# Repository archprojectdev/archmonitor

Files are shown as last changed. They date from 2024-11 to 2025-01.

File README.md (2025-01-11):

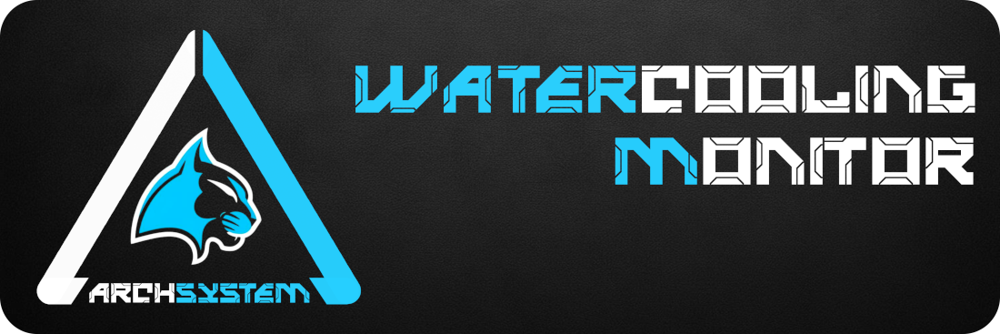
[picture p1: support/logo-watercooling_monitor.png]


Archmonitor est un module de gestion autonome de refroidissement liquide. 
Cette première version beta fonctionne sur un `Raspberry PI 4B` et prend en charge la configuration suivante :

- Deux pompes
- Deux sondes pour la température de liquide
- Une sonde pour le boitier
- Trois circuits indépendants de cinq ventilateurs
- Un circuit global `ARGB2`
- Un écran tactile de contrôle

Les configurations possibles sous cette version sont de :

- Deux modes de refroidissement configurable
- Trois modes configurables pour le circuit `ARGB2`

Le logiciel Archmonitor est basé sur la surcouche `ArchGUI` lui-même basé sur `FreeSimpleGUI` et sur `ws2812.py`. 
Ce programme fonctionne sur un `Raspberry PI 4B` avec le dernier `Raspberry Pi OS 64Bits` comme OS.<br/><br/>

⚠️ Ce module est encore en phase beta. De nombreuses améliorations et possibilités vont être apportées dans les mois à venir.<br/><br/>
Les améliorations déjà prévues sont : 

- Une configuration de plusieurs modes lumineux supplémentaires directement via l’écran tactile.
- Une gestion des modes lumineux par rapport au démarrage et à l’arrêt de l’ordinateur.
- Configuration des modes `silent` et `performance` via l’écran tactile.
- Démarrage de l’ordinateur via l’écran tactile.
- Ajout d’un second circuit ARGB2 pour avoir deux gestions lumineuses en tandem.
- Ajout d’un second écran pour l’affichage de données ou personnage animé.

<br/>

| Boitier prototype fermé | Boitier prototype ouvert |
|---|---|
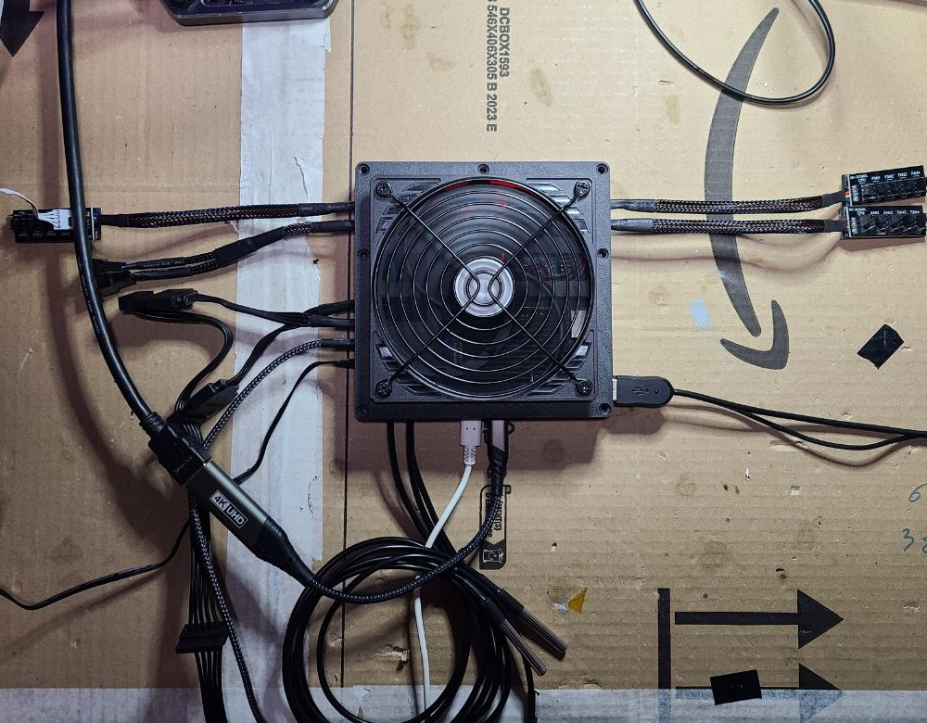
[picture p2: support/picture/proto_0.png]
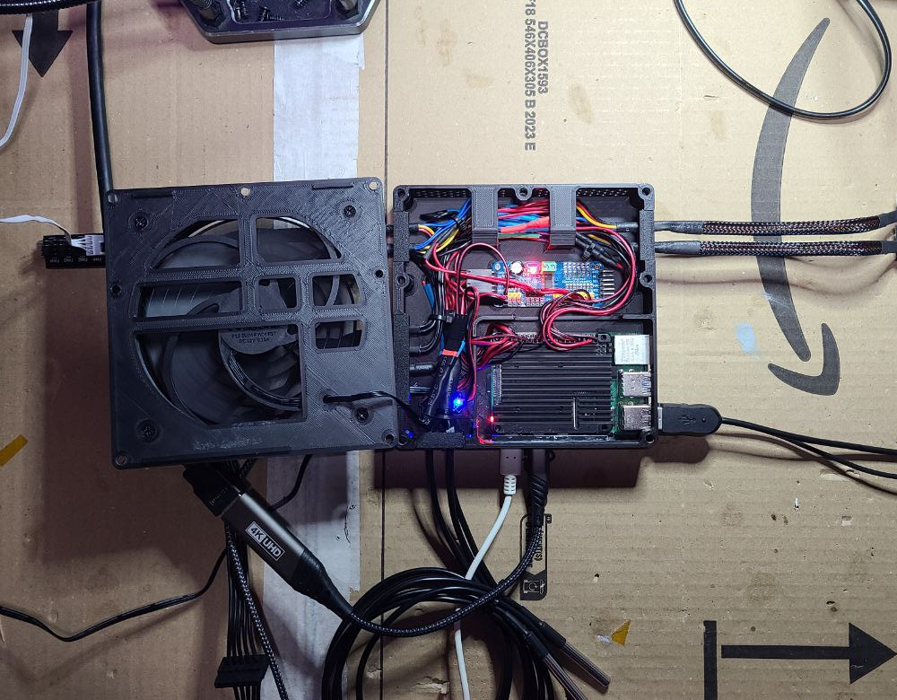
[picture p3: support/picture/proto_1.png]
|  |  |

| Affichage sur écran tactile | STL disponible pour impression 3D |
|---|---|
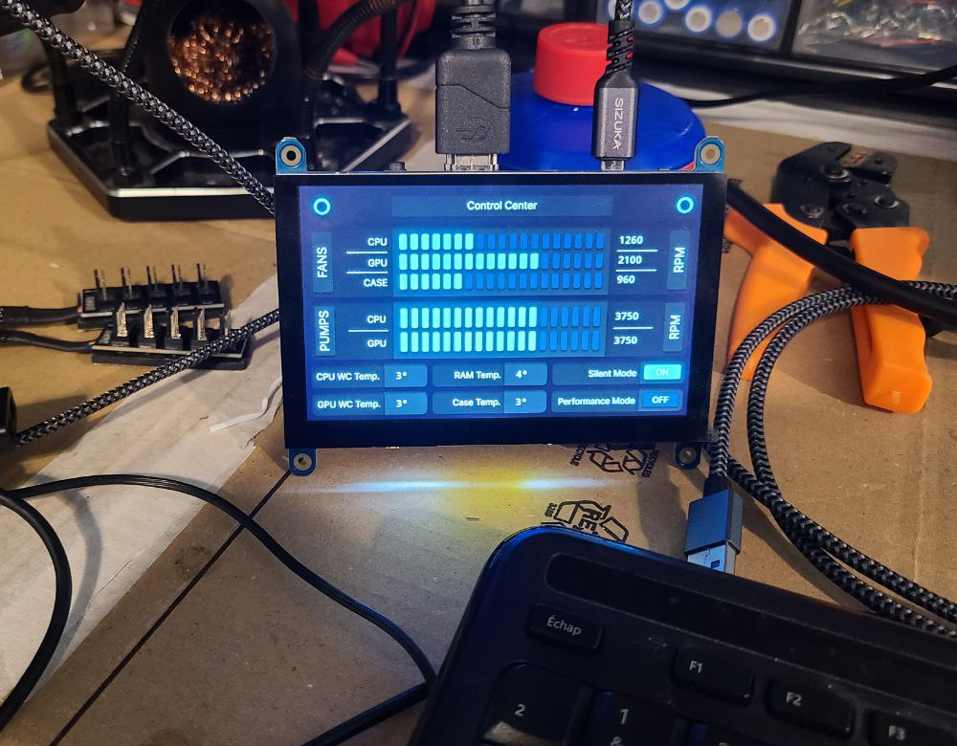
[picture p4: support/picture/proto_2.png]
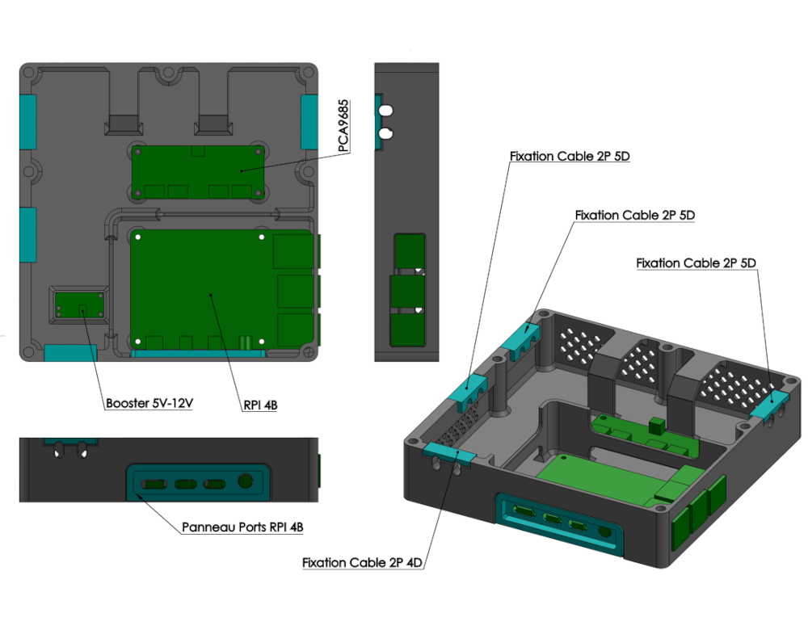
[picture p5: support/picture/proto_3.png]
|  |  |

<br/>

Ces photos sont faites à partir du prototype. Elles ne sont plus à jour.<br/>
Je referais des photos à la prochaine version dans de bonnes conditions.

<br/>

## 😊 Alimentation et principe de fonctionnement :

### Les alimentations :

Le Raspberry PI est alimenté par un USB3.2 interne de la carte mère.
Il faut veiller à ce que les ports USB reste alimenté après l’arrêt de l’ordinateur, voir dans le BIOS pour paramétrer 
cela si ce n’est pas d’usine.<br/>

L’écran est alimenté via un USB dédier du Raspberry PI ou via l’USB du tactile selon les modèles.<br/>

Le ventilateur du Raspberry est alimenté via le 5 V du PI élevé à 12 V via le boosteur, voir les câblages dans la partie dédiée ci-dessous.

Les HUBs des ventilateurs ainsi que les deux 4-Pins des pompes sont alimentés via le cable SATA de l’alimentation de l’ordinateur. Ils ne sont donc pas alimentés lorsque l’ordinateur est éteint.

Le circuit ARGB2 est alimenté via l’USB qui alimente le PI, le circuit ARGB2 reste donc alimenté une fois l’ordinateur éteint.

### Le fonctionnement :

Le Raspberry PI et l’écran restent toujours alimenté. L’écran peut donc piloter l’Archmonitor avec le PC éteint pour gérer le circuit ARGB2.
Une fois l’ordinateur démarré, le Raspberry PI contrôle les signaux PWM des différentes pompes et HUBs de ventilateur par rapport aux paramètres donnés dans le fichier `config.json` et aux températures récupérées par les sondes.

<br/>

## 🛠️ Lien externe :

- [`Raspberry Pi OS`](https://www.raspberrypi.com/software/)
- [`ws2812-spi`](https://github.com/joosteto/ws2812-spi)

<br/>

## 🛠️ Matériel manufacturé :

| Pièces | Aperçu | Achat |
|---|---|---|
| 1x Raspberry PI 4B | [`Image`](https://github.com/archprojectdev/archmonitor/blob/main/support/preview/RPI4B.png) | [`Amazon`](https://www.amazon.fr/dp/B09TTNF8BT) |
| 1x Dissipateur | [`Image`](https://github.com/archprojectdev/archmonitor/blob/main/support/preview/heat_sink.png) | [`Amazon`](https://www.amazon.fr/dp/B08N617L1J) |
| 1x PAD Cuivre 1.5mm | [`Image`](https://github.com/archprojectdev/archmonitor/blob/main/support/preview/pad_cuivre.png) | [`Amazon`](https://www.amazon.fr/dp/B07G73J1T8) |
| 1x Ventilateur 120mm | [`Image`](https://github.com/archprojectdev/archmonitor/blob/main/support/preview/120mm.png) | [`Amazon`](https://www.amazon.fr/dp/B09RWTCXRR) |
| 1x Contrôleur PCA9685 | [`Image`](https://github.com/archprojectdev/archmonitor/blob/main/support/preview/PCA9685.png) | [`Amazon`](https://www.amazon.fr/dp/B072N8G7Y9) |
| 1x Boosteur 5v-12v | [`Image`](https://github.com/archprojectdev/archmonitor/blob/main/support/preview/boosteur_5v_12v.png) | [`Amazon`](https://www.amazon.fr/dp/B0CW9P4CQP) |
| 3x Sonde DS18B20 | [`Image`](https://github.com/archprojectdev/archmonitor/blob/main/support/preview/DS18B20.png) | [`Amazon`](https://www.amazon.fr/dp/B075FYYLLV) |
| 3x HUBS FAN 4 PINS | [`Image`](https://github.com/archprojectdev/archmonitor/blob/main/support/preview/hub_fan.png) | [`Amazon`](https://www.amazon.fr/dp/B08XWWXBYD) |
| 2x Cables FAN 4 PINS | [`Image`](https://github.com/archprojectdev/archmonitor/blob/main/support/preview/cable_4_pins.png) | [`Amazon`](https://www.amazon.fr/dp/B01N1Z3FYD) |
| 1x HUB ARGB2 + Cable | [`Image`](https://github.com/archprojectdev/archmonitor/blob/main/support/preview/hub_argb2_cable.png) | [`Amazon`](https://www.amazon.fr/dp/B0D2SMNKZY) |
| 1x Écran 800x480 | [`Image`](https://github.com/archprojectdev/archmonitor/blob/main/support/preview/screen_800x480.png) | [`Amazon`](https://www.amazon.fr/dp/B096ZSZFC8) |
| 1x Cable Micro HDMI | [`Image`](https://github.com/archprojectdev/archmonitor/blob/main/support/preview/cable_microHDMI.png) | [`Amazon`](https://www.amazon.fr/dp/B09J4HMP25) |
| 1x Cable USB 3.2 | [`Image`](https://github.com/archprojectdev/archmonitor/blob/main/support/preview/USB3.2.png) | [`Amazon`](https://www.amazon.fr/dp/B0BWHZBPGJ) |
| 2x Cable USB-A Mini-B | [`Image`](https://github.com/archprojectdev/archmonitor/blob/main/support/preview/usbaminib.png) | [`Amazon`](https://www.amazon.fr/dp/B089F9V5GK) |
| 1x Cable extension SATA | [`Image`](https://github.com/archprojectdev/archmonitor/blob/main/support/preview/sata_power.png) | [`Amazon`](https://www.amazon.fr/dp/B07C71J8LL) |

<br/>

⚠️ Les liens vers Amazon sont le matériel que j’ai utilisé, c’est simplement indicatif.<br/>
⚠️ Suivant l’écran utilisé les câbles nécessaires peuvent varier.

<br/>

## 🛠️ Impression 3D :

| Pièces | Fichiers |
|---|---|
| 1x Boitier | [`Plan PDF`](https://github.com/archprojectdev/archmonitor/blob/main/support/blueprint/Boitier/Boitier.pdf) - [`STL`](https://github.com/archprojectdev/archmonitor/blob/main/support/blueprint/Boitier/Boitier.STL) |
| 1x Couvercle | [`Plan PDF`](https://github.com/archprojectdev/archmonitor/blob/main/support/blueprint/Couvercle/Couvercle.pdf) - [`STL`](https://github.com/archprojectdev/archmonitor/blob/main/support/blueprint/Couvercle/Couvercle.STL) |
| 1x Fixation_Cable_2P_4D | [`Plan PDF`](https://github.com/archprojectdev/archmonitor/blob/main/support/blueprint/Fixation_Cable_2P_4D/Fixation_Cable_2P_4D.pdf) - [`STL`](https://github.com/archprojectdev/archmonitor/blob/main/support/blueprint/Fixation_Cable_2P_4D/Fixation_Cable_2P_4D.STL) |
| 3x Fixation_Cable_2P_5D | [`Plan PDF`](https://github.com/archprojectdev/archmonitor/blob/main/support/blueprint/Fixation_Cable_2P_5D/Fixation_Cable_2P_5D.pdf) - [`STL`](https://github.com/archprojectdev/archmonitor/blob/main/support/blueprint/Fixation_Cable_2P_5D/Fixation_Cable_2P_5D.STL) |
| 1x Panneau_Ports_RPI_4B | [`Plan PDF`](https://github.com/archprojectdev/archmonitor/blob/main/support/blueprint/Panneau_Ports_RPI_4B/Panneau_Ports_RPI_4B.pdf) - [`STL`](https://github.com/archprojectdev/archmonitor/blob/main/support/blueprint/Panneau_Ports_RPI_4B/Panneau_Ports_RPI_4B.STL) |

Plan de montage général : [`Plan PDF`](https://github.com/archprojectdev/archmonitor/blob/main/support/blueprint/Archmonitor.pdf)<br/><br/>
⚠️ Le PAD de cuivre n’est pas visible sur le plan. Il prend place dans l'encoche du boitier sous le PI avec un PAD thermique en silicone entre le PI et le PAD en cuivre.

<br/>

## 🛠️ Câblage :

| Circuit | Fichiers |
|---|---|
| Général | [`Plan PDF`](https://github.com/archprojectdev/archmonitor/blob/main/support/circuit/General.pdf) |
| RPI | [`Plan PDF`](https://github.com/archprojectdev/archmonitor/blob/main/support/circuit/RPI.pdf) |
| Sensors | [`Plan PDF`](https://github.com/archprojectdev/archmonitor/blob/main/support/circuit/Sensors.pdf) |

<br/>

## 💻️ Installation de Raspberry Pi OS :
 - Configuration de l’installation via `Raspberry PI Imager` sur Ubuntu ou une autre distribution
 - Installation de `Raspberry Pi OS 64Bits` sur la carte SD
 - Démarrage du PI

Pour plus de simplicité j’utilise l’user `archmonitor`, vous le retrouvez dans les commandes à venir.

<br/>

## 💻 Mise à jour :
```bash
sudo apt-get update && sudo apt-get upgrade
sudo rpi-update
sudo reboot
```

<br/>

## 💻 Activation des ports :

Puis activez dans `Interface Options` les options suivantes :
```bash
sudo raspi-config
     └── Interface Options
         ├── SPI    : Enabled
         └── 1-Wire : Enabled
```

```bash
sudo modprobe w1-gpio
sudo modprobe w1-therm
```

<br/>

## 💻 Modification des fichiers boot :

### 📄 `/boot/firmware/cmdline.txt` ➡️ [`cmdline.txt`](https://github.com/archprojectdev/archmonitor/blob/main/support/file/cmdline.txt)<br>
```bash
sudo nano /boot/firmware/cmdline.txt
```
Ajouter à la fin de la ligne :
```bash
consoleblank=0 spidev.bufsiz=250000
```

### 📄 `/boot/firmware/config.txt` ➡️ [`config.txt`](https://github.com/archprojectdev/archmonitor/blob/main/support/file/config.txt)<br>
```bash
sudo nano /boot/firmware/config.txt
```
En dessous de `# Uncomment some or all of these to enable the optional hardware interfaces`<br>
Modifier le fichier pour obtenir :
```bash
# Uncomment some or all of these to enable the optional hardware interfaces
dtparam=spi=on
dtparam=i2c_arm=on
```
À la fin du fichier après `[all]`<br>
Modifier le fichier pour obtenir :
```bash
[all]
dtoverlay=w1-gpio,gpiopin=4,disable-bt
display_auto_detect=1

force_turbo=1
core_freq=500 
core_freq_min=500

hdmi_cvt=800 480 60 3 0 0 0
hdmi_group=1
hdmi_mode=14
hdmi_boost=7

framebufferheight=480
framebufferwidth=800
```

### Redémarrer le PI : <br>
```bash
sudo reboot
```

<br/>

## 💻 Test de détection des sondes :
```bash
cd /sys/bus/w1/devices/
ls
```

 ```
28-xxxxxxxxxxxx  28-xxxxxxxxxxxx  28-xxxxxxxxxxxx  w1_bus_master1
```

Vous devez voir trois devices commençant par `28-xxxxxxxxxxxx`.<br/>
Rentrez dans une de ces devices afficher les données de la sonde :

```bash
cd 28-xxxxxxxxxxxx
cat w1_slave
```

```bash
52 01 55 00 7f ff 0c 10 53 : crc=53 YES
52 01 55 00 7f ff 0c 10 53 t=21125
```

La deuxième ligne vous indiquera la température de la sonde en millième de degré : `t=21125`<br/>
La sonde indique 21 degrés : `21125 / 100 = 21`

## 💻 Installation des librairies Python :
```bash
sudo apt-get install pigpio python3-pigpio
sudo systemctl enable pigpiod
sudo systemctl start pigpiod 

sudo pip3 install --break-system-packages FreeSimpleGUI pynput screeninfo gpiozero
sudo pip3 install --break-system-packages adafruit-circuitpython-pca9685

sudo reboot
```

<br/>

## 💻 Téléchargement :
📂 Dans le `home` de votre `user`:
```bash
wget https://github.com/archprojectdev/archmonitor/archive/refs/heads/main.zip
unzip main.zip

mv archmonitor-main archmonitor
cd archmonitor

wget https://github.com/archprojectdev/archgui/archive/refs/heads/main.zip
unzip main.zip

mv archgui-main archgui
```

```bash
/home/archmonitor/archmonitor/

├── archgui
│   ├── config
│   │   └── default.json
│   │
│   ├── __init__.py
│   ├── Interpreter.py
│   ├── Model.py
│   ├── README.md
│   ├── Windows.py
│   └── Workarea.py
│   
├── archgui_events
│   └── main.py
│   
├── archgui_windows
│   └── main.json
│   
├── resource
├── support
│   
├── config.json
├── Display.py
├── Listener.py
├── main.py
├── README.md
├── sensors.py
├── Spiled.py
└── Temperature.py
```

<br/>

## 💻 Configuration :
📂 Dans le `home` de votre `user`:
```bash
cd archmonitor
python sensors.py
```
```bash
----------------------------------------------
/sys/bus/w1/devices/28-7f79541f64ff/w1_slave - 21
/sys/bus/w1/devices/28-837e541f64ff/w1_slave - 25
/sys/bus/w1/devices/28-d97b541f64ff/w1_slave - 21
```
Avec une source de chaleur, 
faites varier la température de chaque sondes pour déterminer quelle sonde correspond à quel ID.<br/>
Une fois déterminé, modifiez le fichier `/home/archmonitor/archmonitor/config.json` en conséquence :
```bash
"sensors": {
  "wc_cpu": "/sys/bus/w1/devices/28-7f79541f64ff/w1_slave",
  "wc_gpu": "/sys/bus/w1/devices/28-837e541f64ff/w1_slave",
  "case": "/sys/bus/w1/devices/28-d97b541f64ff/w1_slave"
}
```
<br/>

## 💻 Test :
```bash
cd archmonitor
python main.py
```

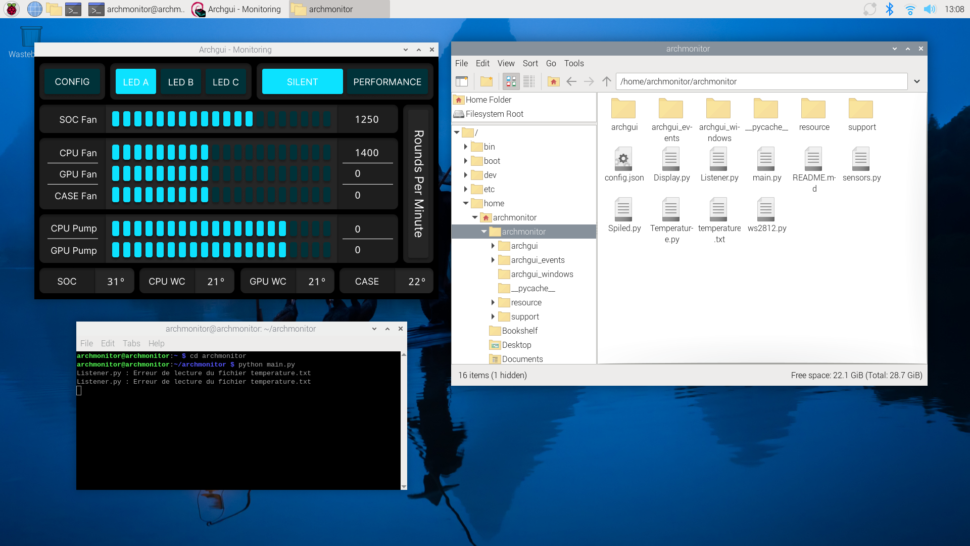
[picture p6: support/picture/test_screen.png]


<br/>
Comme vous pouvez le constater, les erreurs d’écriture/lecture des températures sont fréquentes pour le moment, mais ne posent aucun problème, cela vient de la concurrence entre le process de récupération et l'utilisation du fichier temporaire. Je trouverais une solution plus élégante à l'avenir. 

<br/>
<br/>

## 💻 Création des fichiers Xorg :
### 📄 `/etc/X11/xorg.conf.d/10-blanking.conf` ➡️ [`10-blanking.conf`](https://github.com/archprojectdev/archmonitor/blob/main/support/file/10-blanking.conf)<br>

```bash
sudo nano /etc/X11/xorg.conf.d/10-blanking.conf
```
```bash
Section "Extensions"
    Option      "DPMS" "Disable"
EndSection

Section "ServerLayout"
    Identifier "ServerLayout0"
    Option "StandbyTime" "0"
    Option "SuspendTime" "0"
    Option "OffTime"     "0"
    Option "BlankTime"   "0"
EndSection
```

### 📄 `/etc/X11/xorg.conf.d/10-monitor.conf` ➡️ [`10-monitor.conf`](https://github.com/archprojectdev/archmonitor/blob/main/support/file/10-monitor.conf)<br>
```bash
sudo nano /etc/X11/xorg.conf.d/10-monitor.conf
```
```bash
Section "Monitor"
    Identifier "XWAYLAND0"
    Modeline "800x480_60.00"   29.50  800 824 896 992  480 483 493 500 -hsync +vsync
    Option "PreferredMode" "800x480_60.00"
EndSection

Section "Screen"
    Identifier "HDMI-A-1"
    Monitor "XWAYLAND0"
    DefaultDepth 24
    SubSection "Display"
        Modes "800x480_60.00"
    EndSubSection
EndSection
```

<br/>

## 💻 Création des fichiers de lancement :
### 📄 Créer le fichier : `/home/archmonitor/.bashrc`
```bash
nano .bashrc
>> bash startx.sh
```
### 📄 Créer le fichier : `/home/archmonitor/startx.sh`
```bash
nano startx.sh
>> cd /home/archmonitor/archmonitor
>> startx
```
### 📄 Créer le fichier : `/home/archmonitor/.xinitrc`
```bash
nano .xinitrc
>> exec python /home/archmonitor/archmonitor/main.py
```

<br/>

## 💻 Redémarrage :

Démarrage en mode console avec autologin.

```bash
sudo raspi-config
     └── systeme
         └── boot / Autologin
             └── console Autologin

sudo reboot
```

Si tout c’est bien passé, vous devez arriver sur l’interface de l’Archmonitor.

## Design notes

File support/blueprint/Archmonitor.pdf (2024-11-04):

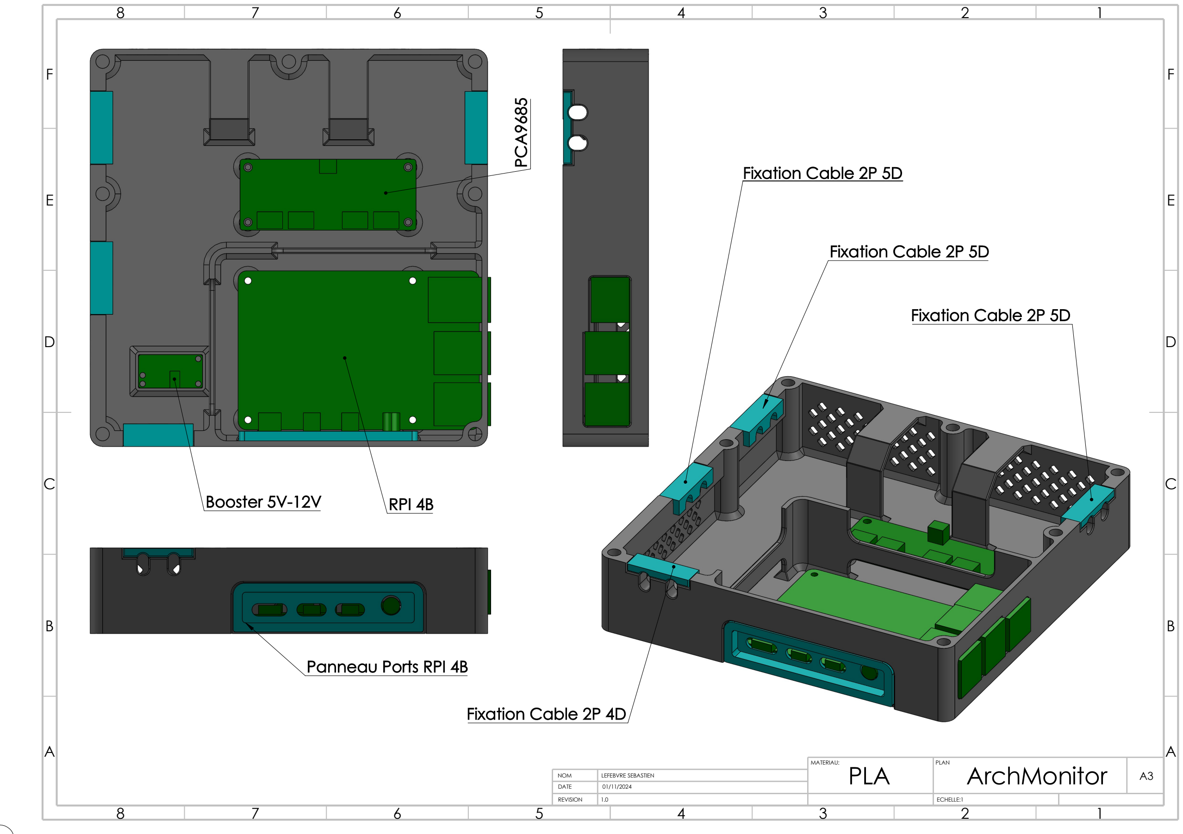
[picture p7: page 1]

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
MATERIAU: PLA | PLAN ArchMonitor | A3
NOM | 01/11/2024 LEFEBVRE SEBASTIEN

DATE

REVISION | 1.0 | ECHELLE:1
Booster 5V-12V | RPI 4B | PCA⁹⁶⁸⁵

Fixation Cable 2P 5D

Fixation Cable 2P 5D

Fixation Cable 2P 5D

Fixation Cable 2P 4D

Panneau Ports RPI 4B

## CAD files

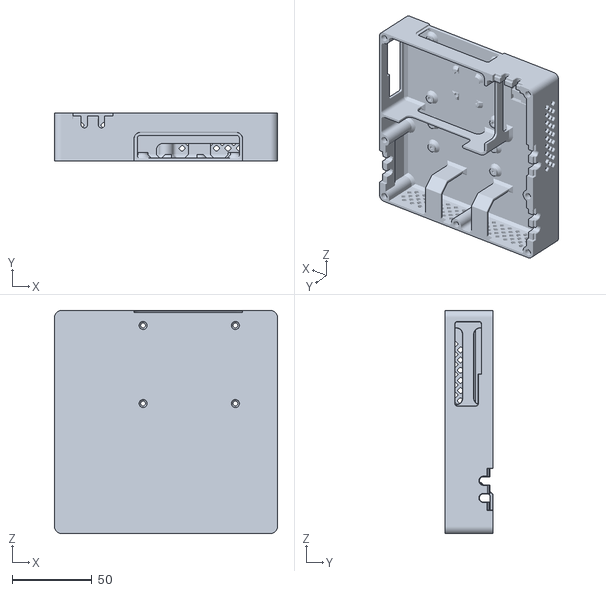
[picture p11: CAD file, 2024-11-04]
support/blueprint/Boitier/Boitier.STL
140.0 x 30.2 x 140.0

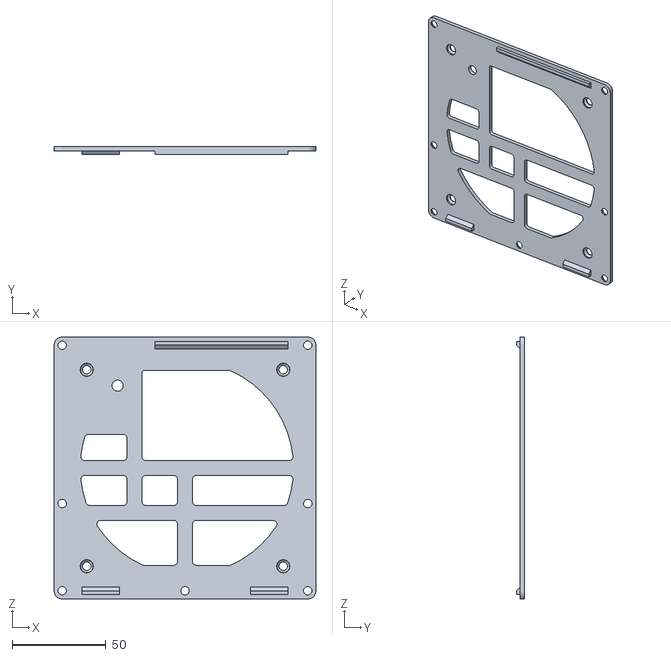
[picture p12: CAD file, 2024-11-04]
support/blueprint/Couvercle/Couvercle.STL
140.0 x 4.40 x 140.0

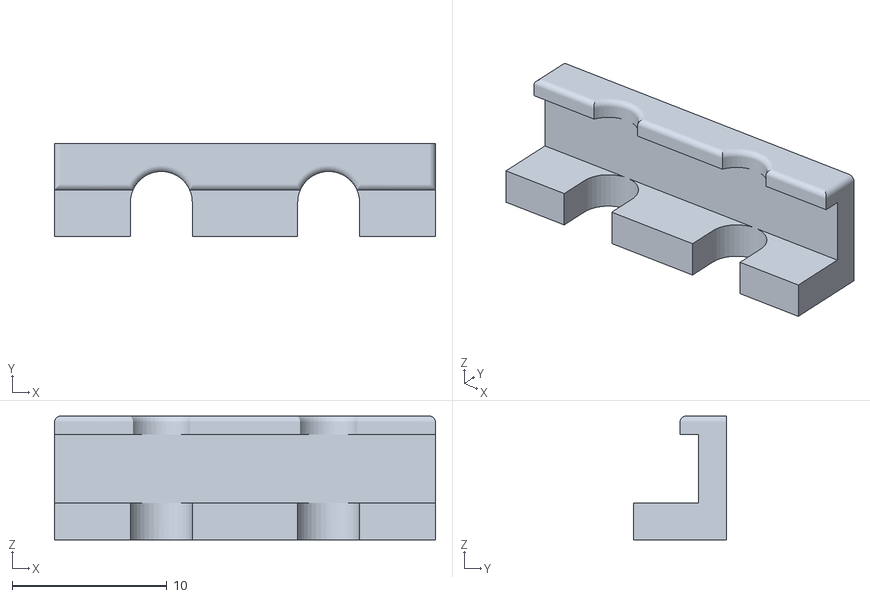
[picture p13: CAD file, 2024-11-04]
support/blueprint/Fixation_Cable_2P_4D/Fixation_Cable_2P_4D.STL
24.6 x 6.00 x 8.00

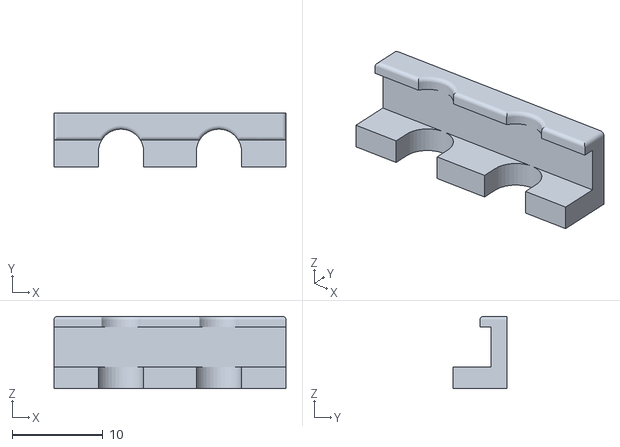
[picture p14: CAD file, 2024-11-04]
support/blueprint/Fixation_Cable_2P_5D/Fixation_Cable_2P_5D.STL
25.6 x 6.00 x 8.00

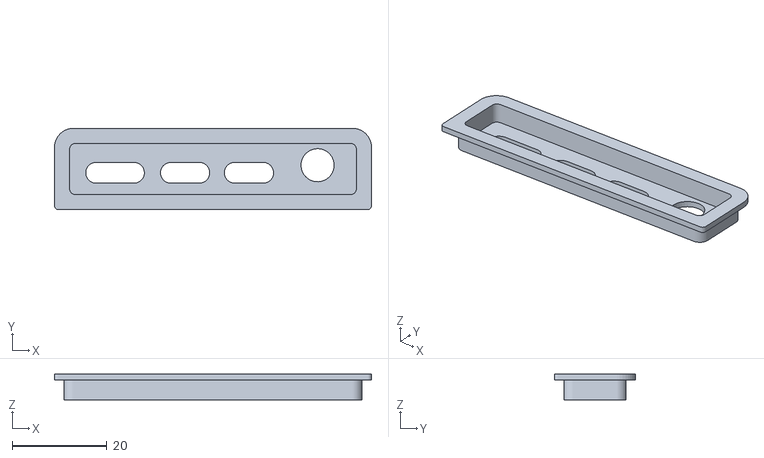
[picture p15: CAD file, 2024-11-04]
support/blueprint/Panneau_Ports_RPI_4B/Panneau_Ports_RPI_4B.STL
67.0 x 17.2 x 5.40

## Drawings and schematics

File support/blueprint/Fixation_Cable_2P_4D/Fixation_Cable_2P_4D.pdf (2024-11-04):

E E

F F

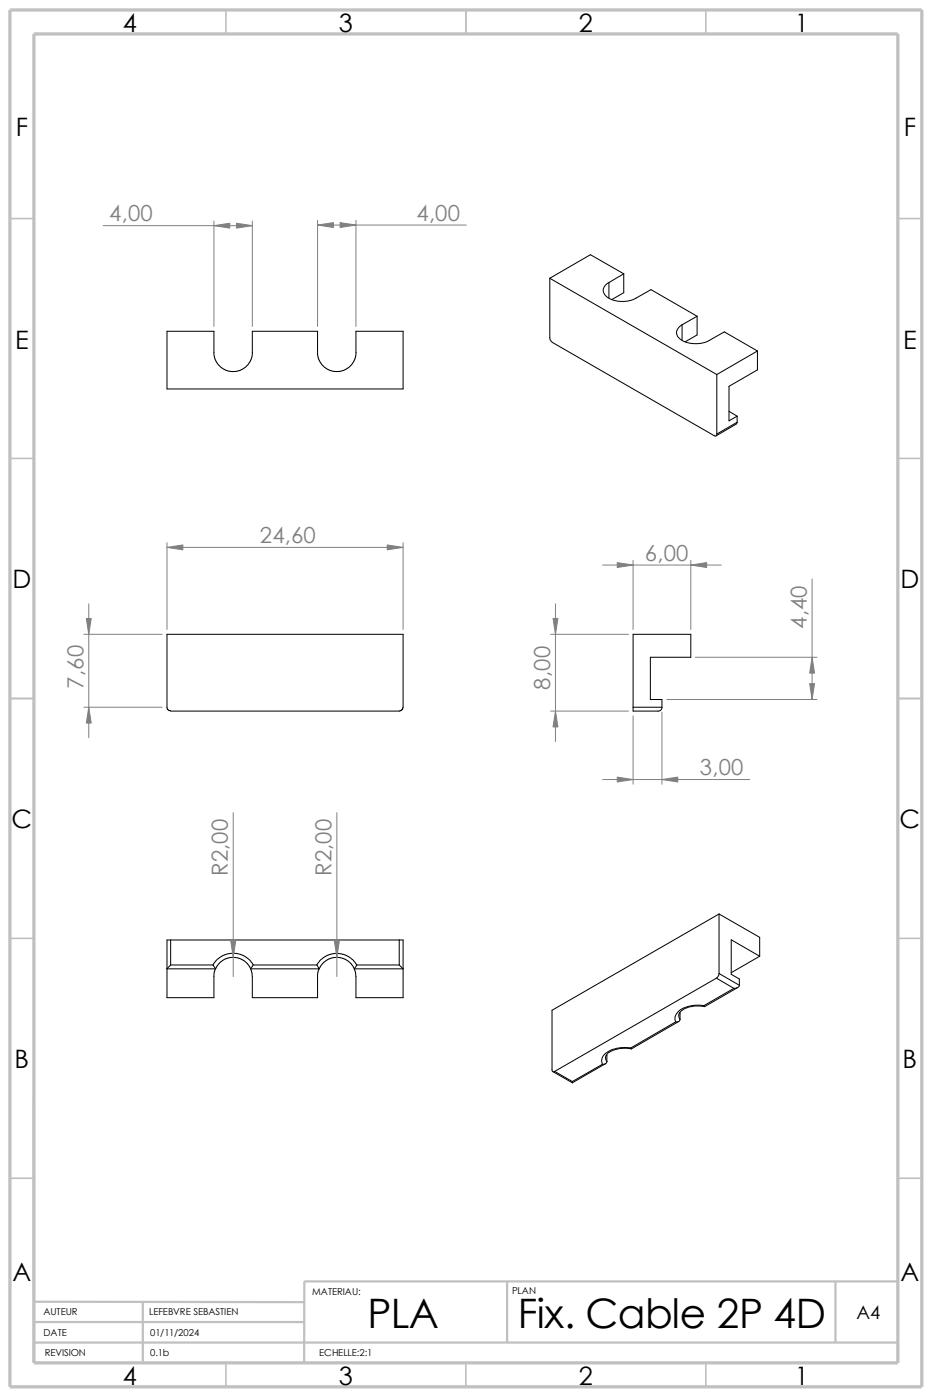
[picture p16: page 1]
LEFEBVRE SEBASTIEN; PLA R2,00

MATERIAU: | PLAN Fix. Cable 2P 4D | A4
AUTEUR

DATE | 01/11/2024
REVISION | 0.1b | ECHELLE:2:1

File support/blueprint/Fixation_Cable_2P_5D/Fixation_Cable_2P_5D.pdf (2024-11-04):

E E

F F

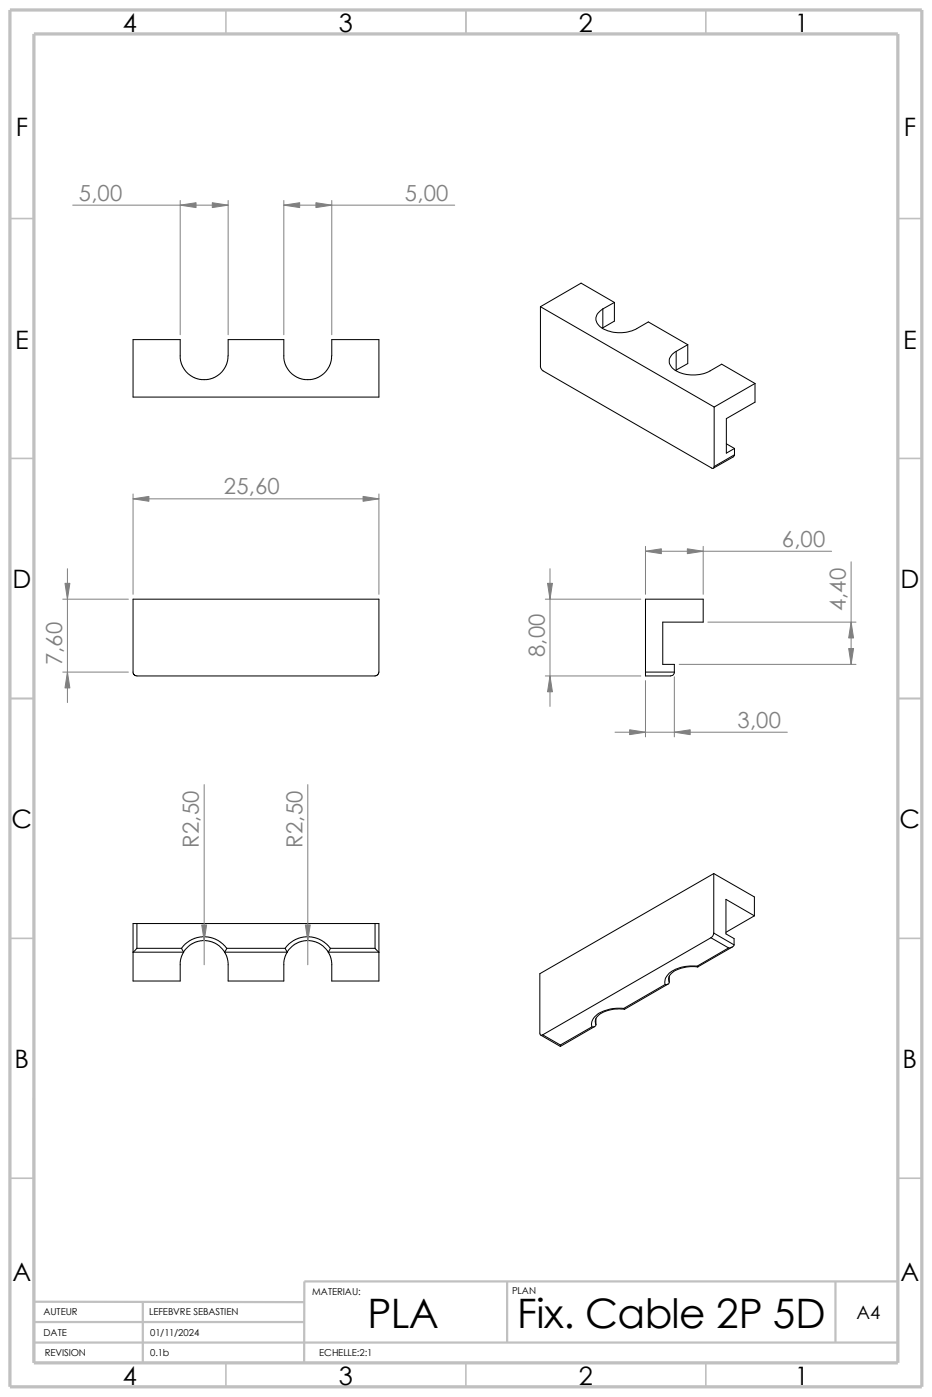
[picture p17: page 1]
PLA R2,50

MATERIAU: | PLAN Fix. Cable 2P 5D | A4
AUTEUR | LEFEBVRE SEBASTIEN

DATE | 01/11/2024
REVISION | 0.1b | ECHELLE:2:1

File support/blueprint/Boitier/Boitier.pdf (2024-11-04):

E E

F F

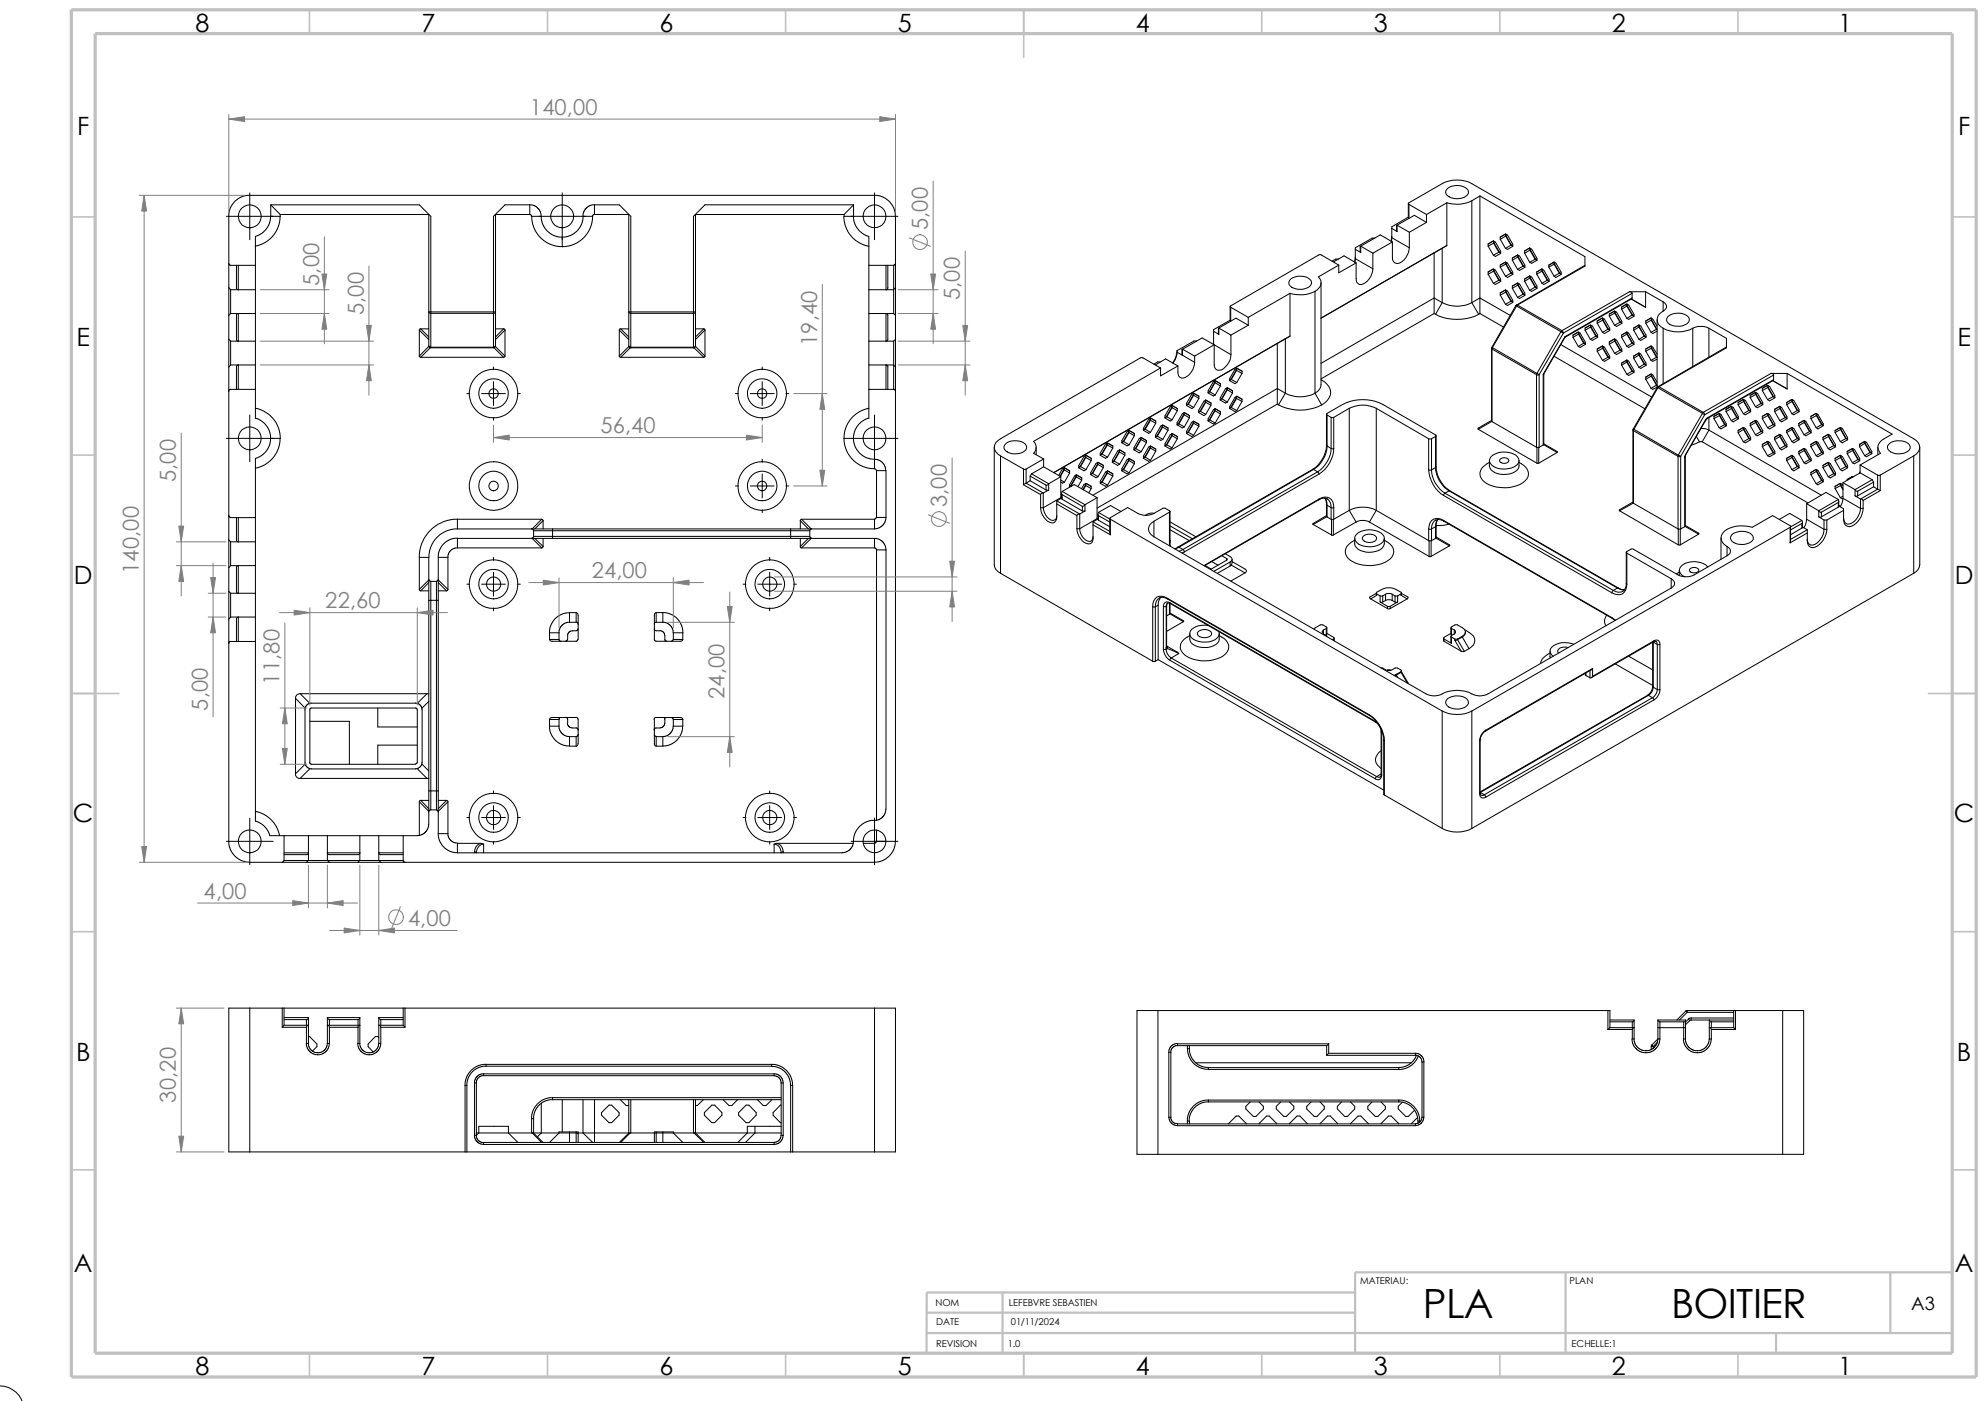
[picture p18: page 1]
BOITIER ³⁰,20 140,00

MATERIAU: PLA | PLAN | A3
NOM | LEFEBVRE SEBASTIEN

DATE

REVISION | 1.0 | ECHELLE:1

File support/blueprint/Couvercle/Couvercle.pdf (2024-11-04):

E E

F F

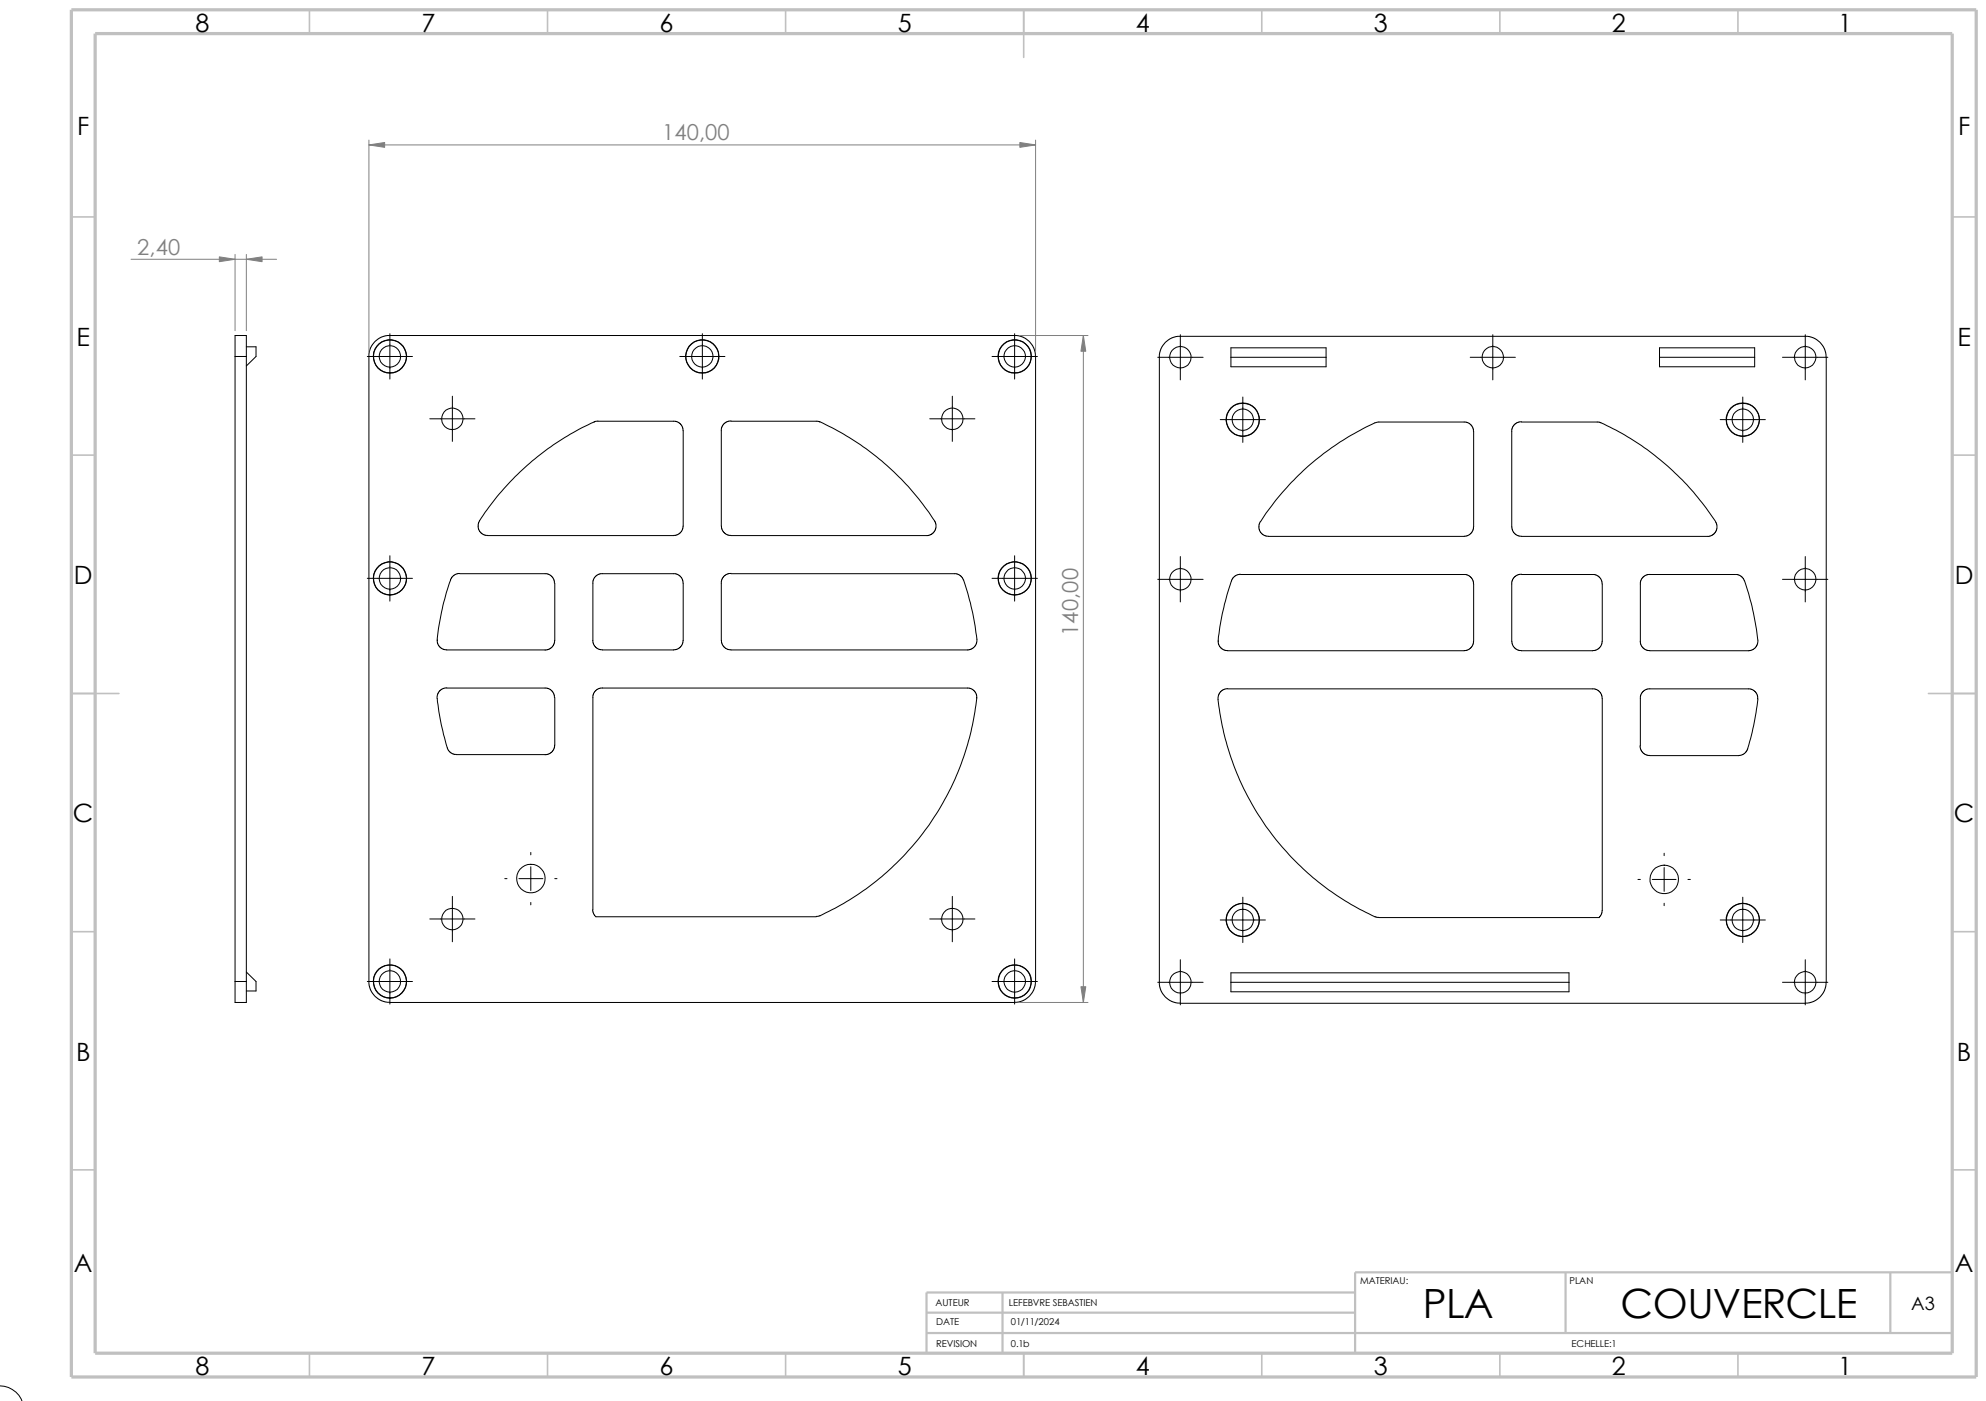
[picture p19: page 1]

MATERIAU: PLA | PLAN COUVERCLE | A3
AUTEUR | 01/11/2024 LEFEBVRE SEBASTIEN

DATE

REVISION | 0.1b | ECHELLE:1

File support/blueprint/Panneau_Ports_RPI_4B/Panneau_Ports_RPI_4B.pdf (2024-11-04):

E E

F F

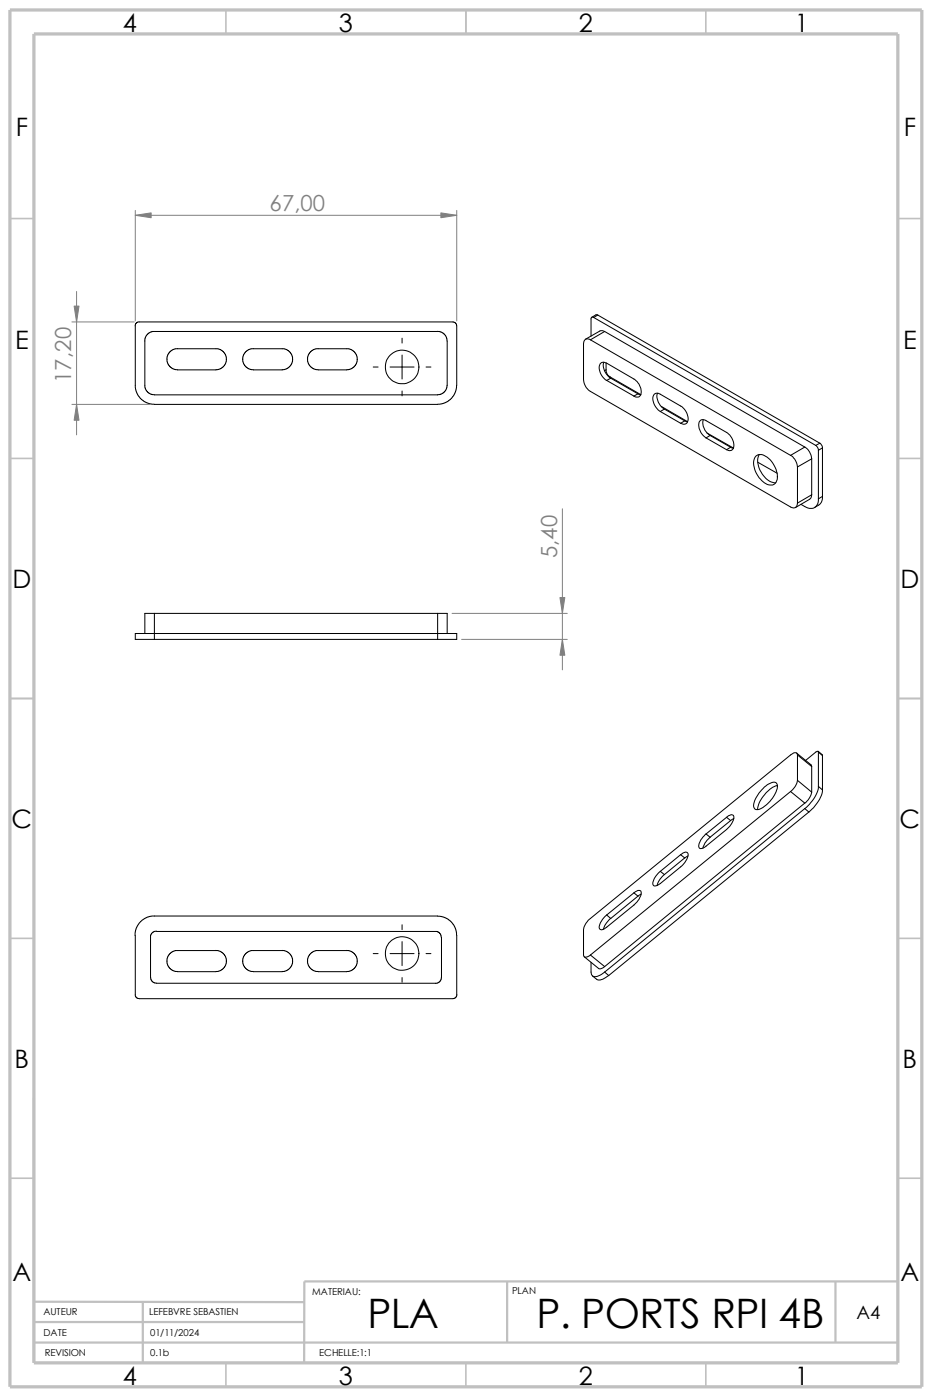
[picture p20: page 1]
LEFEBVRE SEBASTIEN; PLA

MATERIAU: | PLAN P. PORTS RPI 4B | A4
AUTEUR

DATE | 01/11/2024
REVISION | 0.1b | ECHELLE:1:1

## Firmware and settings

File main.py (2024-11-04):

"""
main.py
"""

import os
import sys
import time
import signal
import subprocess
import archgui


from Listener import Listener
from Display import Display
from Spiled import Spiled


if __name__ == "__main__":

    display = Display()
    listener = Listener()
    spiled = Spiled()

    modules = {
        "archgui": archgui,
        "display": display,
        "listener": listener,
        "spiled": spiled
    }

    cmd_temperature = ['python', 'Temperature.py']
    pro_temperature = subprocess.Popen(cmd_temperature)

    def signal_handler(_, __):
        """
        :param _:
        :param __:
        """
        os.killpg(os.getpgid(pro_temperature.pid), signal.SIGTERM)
        # modules["spiled"].exit()
        # modules["listener"].exit()
        # modules["display"].exit()
        # modules["archgui"].exit()
        sys.exit(0)

    while True:
        time.sleep(1)
        if os.path.exists("temperature.txt"):
            break

    archgui.define_modules(modules)
    display.define_modules(modules)
    listener.define_modules(modules)
    spiled.define_modules(modules)

    main_uniqid = archgui.open(model="main", title="Archgui - Monitoring")
    archgui.define_main(main_uniqid)
    archgui.bind(
        uniqid=main_uniqid,
        binds=[
            {
                "item": "graph_interface",
                "bind_string": "<Button-1>",
                "bind_key": " button-1"
            }
        ])

    display.define_graph(main_uniqid, "graph_interface")
    display.generate()

    signal.signal(signal.SIGINT, signal_handler)

    spiled.run()
    listener.run()
    archgui.run()

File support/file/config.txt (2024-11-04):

# For more options and information see
# http://rptl.io/configtxt
# Some settings may impact device functionality. See link above for details

# Uncomment some or all of these to enable the optional hardware interfaces
#dtparam=i2c_arm=on
#dtparam=i2s=on
dtparam=spi=on
dtparam=i2c_arm=on

# Enable audio (loads snd_bcm2835)
dtparam=audio=on

# Additional overlays and parameters are documented
# /boot/firmware/overlays/README

# Automatically load overlays for detected cameras
camera_auto_detect=1

# Automatically load overlays for detected DSI displays
display_auto_detect=1

# Automatically load initramfs files, if found
auto_initramfs=1

# Enable DRM VC4 V3D driver
dtoverlay=vc4-kms-v3d
max_framebuffers=2

# Don't have the firmware create an initial video= setting in cmdline.txt.
# Use the kernel's default instead.
disable_fw_kms_setup=1

# Run in 64-bit mode
arm_64bit=1

# Disable compensation for displays with overscan
disable_overscan=1

# Run as fast as firmware / board allows
arm_boost=1

[cm4]
# Enable host mode on the 2711 built-in XHCI USB controller.
# This line should be removed if the legacy DWC2 controller is required
# (e.g. for USB device mode) or if USB support is not required.
otg_mode=1

[cm5]
dtoverlay=dwc2,dr_mode=host

[all]
dtoverlay=w1-gpio,gpiopin=4,disable-bt
display_auto_detect=1
force_turbo=1
core_freq=500
core_freq_min=500
hdmi_cvt=800 480 60 3 0 0 0
hdmi_group=1
hdmi_mode=14
hdmi_boost=7
framebufferheight=480
framebufferwidth=800
